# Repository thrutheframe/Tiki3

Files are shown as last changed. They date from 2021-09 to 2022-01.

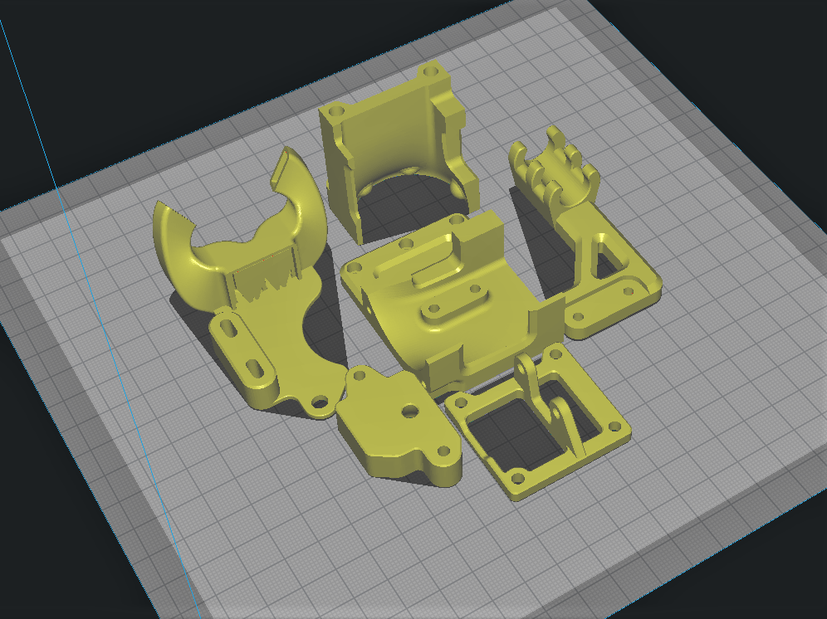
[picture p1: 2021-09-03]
3_2 Print orientation.png

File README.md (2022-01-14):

Tiki3 Gen3 2

# Tiki3 (version 3.2)

<b>Update 14 Jan 2022: </b> ADXL from Aliexpress shops are smaller (16mmx 20.5mm). So I have edited the body top to be able to mount them.  
\
\
\
\
<b>Update 14 Oct 2021: </b> 
- Updated fan duct design to V2. used a CFD simulation to check for air path.
- Added body_top with adxl mount. Mounting holes are 19mm apart. Please measure your adxl to check fitting. Will only work with fan_duct V2. 
body_top adxl04

\
\
<b>Update 12 Sep 2021: </b> shorter version of cable relief added. reduce by 20mm from the original. This is to prevent the cable from hitting the top bar during tall prints. 
\
\
<b>Introduction</b>\
A mount and fan duct system for Creality Ender 3/3pro/3V2 and Ender 5/5plus

This mount and fan duct system is designed for the hotend carriage of some Creality Ender machines.  
- Ender 3/3pro/3V2
- Ender 5/5pro/5plus

Hotend that has been designed for:
- Creality stock CR10 hotend (tested)
- Mellow NF-Zone CR10 (tested)
- Mellow NF-Smart 
- MicroSwiss All Metal and clones
- Red Lizard (need mod)
 
Tiki3 can be used as direct drive system with the Orbiter V1.5 or in a bowden configuration (No need to print "3_2 Orbiter bracket.stl" for bowden config)

A 5015 fan is required as the stock 4010 fan is underpowered for a dual fan duct system. 
 
Please see the other files for print orientation and BOM of screws and nuts required. 
 
There are many mount and fan duct system out there, what I think differs mine from others is the design focus on:
- Printability
- Functionality
- Modular system
 
As with all one-man-show, I would need the help of the community use/test this system and provide constructive suggestion to help me improve the existing design. 
Thank you for visiting my github page. 

I have to give credit where credit was due, so here goes: 

<b>CREDITS:</b>

My wife, for putting up with me as I dive into this insanity of mine. 

20four80five: https://www.thingiverse.com/thing:3354741
For first planting the idea of a side mount cooling fan and front mount part cooling fan

Hangtight: https://www.thingiverse.com/thing:4725293
For using his fan duct in version 3.1 when I was still learning Fusion360 and basing some of the design from him work as they are good.

lorinczroby: https://www.thingiverse.com/thing:4725897
For designing the Orbiter which I used for the direct drive design.

Grabcad community for coming up with all the STEP files that I need ie; 5015, 4010, BL touch, etc

Mellow for sharing with me the STEP file of their NF-Zone hotend. 

Thingiverse and anyone/organisation that I forgot to give credit to.

Please do share your make on Thingiverse: https://www.thingiverse.com/thing:4949727

<b>FAQs:</b>

Q: Is there any major design changes between this version (3.2) and the previous versions that are uploaded on Thingiverse?

A: Most of the changes structual improvements, but the position of the mounting holes are the same. The major changes is the fan duct. but it will still fit the over versions as the mounting holes are the same. 

Q:Will there be a design for V6 /Dragon hotend?

A: Yes. I am working on the Dragon version. You can download it from https://github.com/thrutheframe/Tiki3_Dragon. The V6 version is a bit tricky. so it will take time.

Q: Would you be able to include a custom design for bracket/fan duct/holder etc etc?

A: Due to my engineering background and training, I have a habit to print and test the designs to my level best before I release them. Without the actual item (or part that are close the the same dimensions) I would not be able to do that. Either I can borrow the items from friends or someone/company is willing to sponsor me the item. There is not much I can do. 

Q: Will this system fit the Sovol/Tronxy/TwoTrees etc etc?

A: Honestly, I would not know as I do not have those printers to work with.

Q: Would you release the STEP file for others to remix your design?

A: I asked this question once and the answer was "if u can remix it, u can design it on your own". He was kindof an asshole, but he was not wrong either. That is why I ended up designing my own mount system. I prefer not to be an asshole, but I am cheeky. Hence, I would release the STEP files for the body and BL bracket, which will be a good foundation to built your own version/remix.  

Q: Did you test print it in PLA? How did you get even get such specific numbers? "...I find stuff like this very misleading with serious potential to cause damage to printers when people try to do it..." 

A: I try my best to answer questions pertaining to the design. Constructive suggestions and contributions to the design are greatly apperciated. Please be polite and nice. 

Q: How accurate is the CFD simulation on your fan duct? Did u consider turbulance of of the 5015? Did u take into account of hotend movement? etc etc.

A: My basic CFD simulation of the particles movement (air) is to provide a validation that the air is directed under the nozzle when designing the fan duct. There are many other parameters that I would not know. tbh, it's a fanduct for 3D printer, not a cooling system of a nuclear plant... so take a chill pill and dun go karen/kevin on me. 

Q: Why do you add a heat sink to your motor? it is counter-productive as it add weight? 

A: Simple. I like it. 

Q: Why it is called Tiki3

A: Tiki was the name of our family dog. He passed away several years ago and we still miss him dearly. So I named this system after him. 

<b>Contributions</b>\
 My 3D printing hobby is running on Fun-Funds which is usually in fumes state. Contribution to this funds are from small print jobs, servicing 3D printers and the once-in-a-blue-moon tip to my paypal.me account. If you like using this system and would like to really thanks me, a $2 coffee tip will be greatly appreciated (I like coffee). Thank you. https://www.paypal.com/paypalme/shannonheng

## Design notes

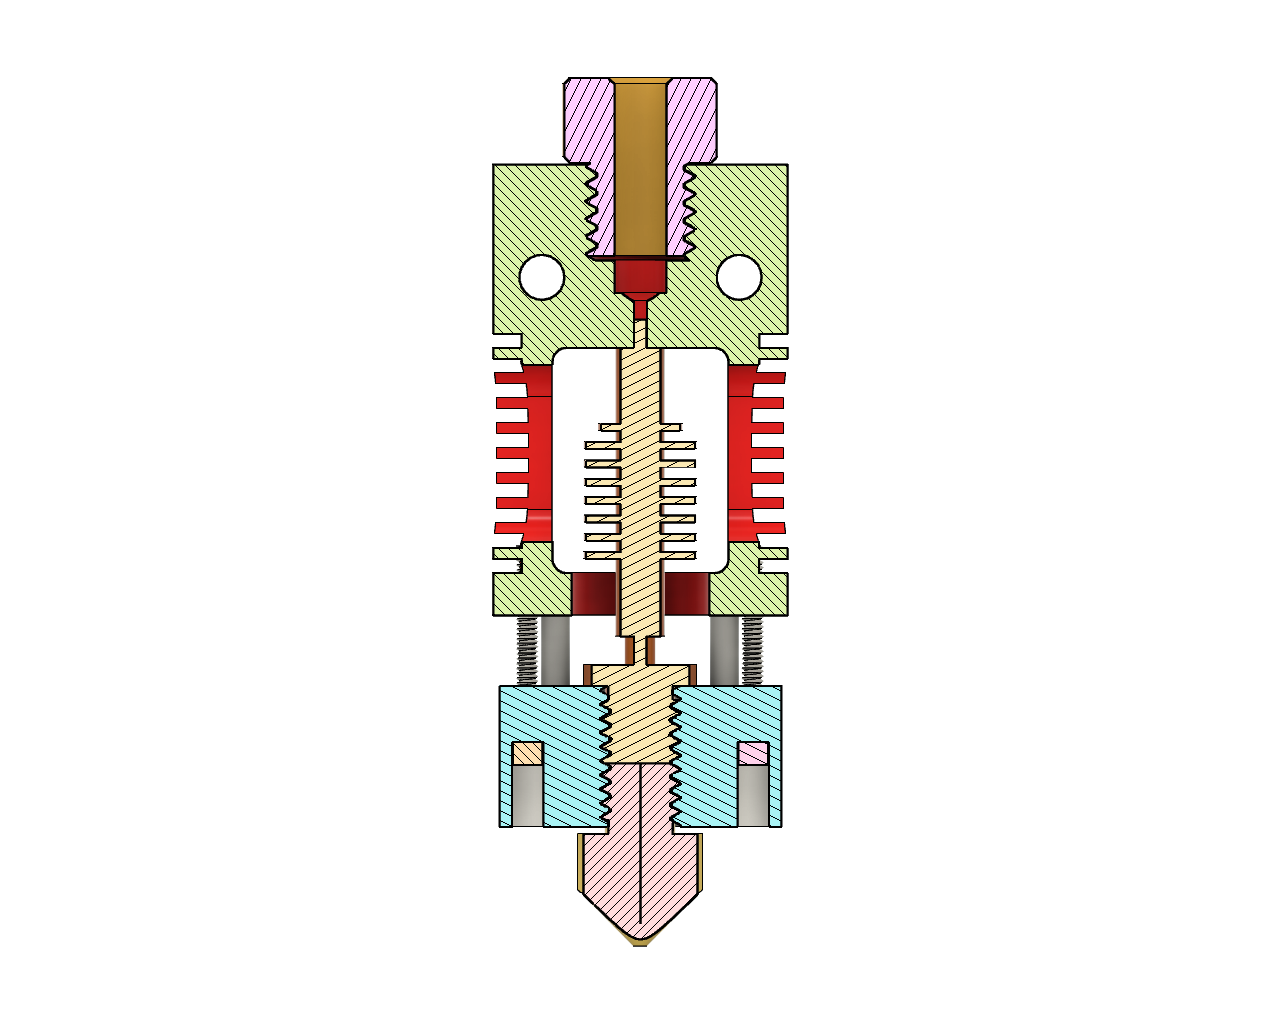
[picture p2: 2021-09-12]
Red Lizard adapter/adapter image 02.png

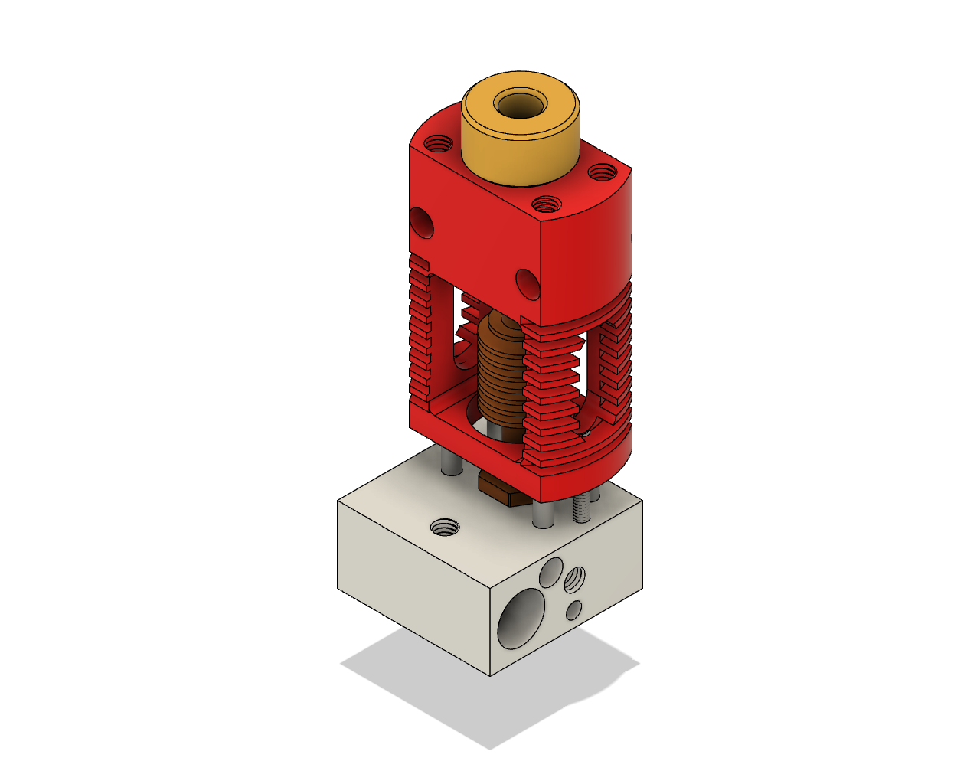
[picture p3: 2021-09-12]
Red Lizard adapter/adapter image 01.png

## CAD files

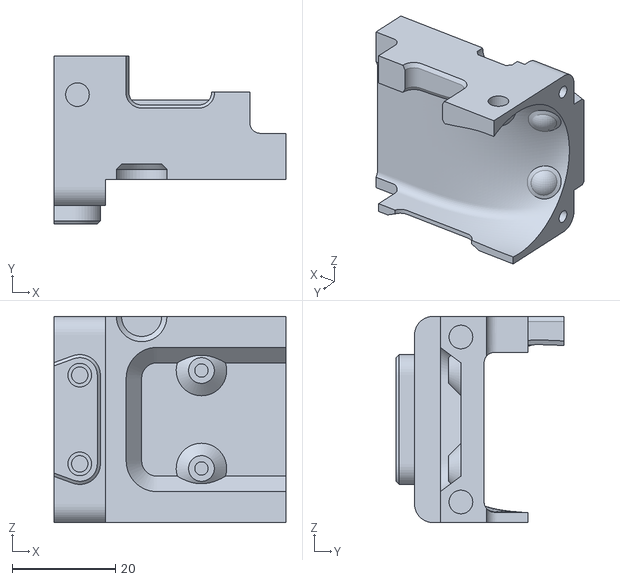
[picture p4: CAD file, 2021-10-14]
3_2 Body for brass inserts/3_2 Body_top adxl.stl
45.0 x 32.6 x 40.0

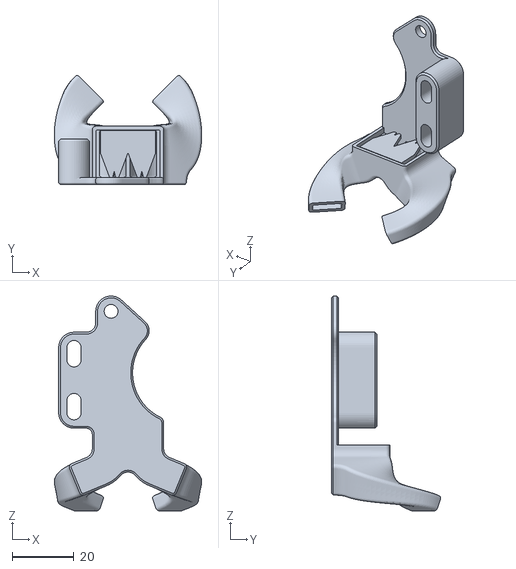
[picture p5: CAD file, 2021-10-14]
3_2 other parts/3_2 Fan_duct V2.stl
47.9 x 35.5 x 69.9

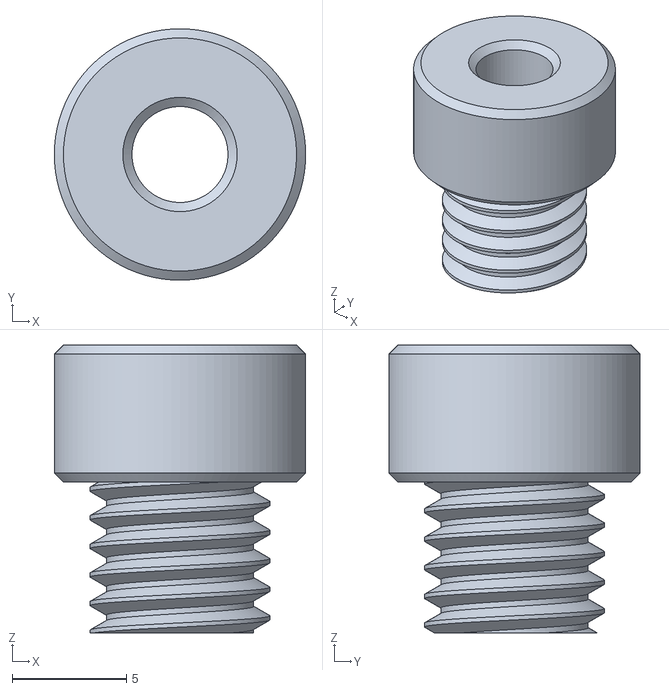
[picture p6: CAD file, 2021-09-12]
Red Lizard adapter/red lizard adapter 01.stl
11.0 x 11.0 x 12.6

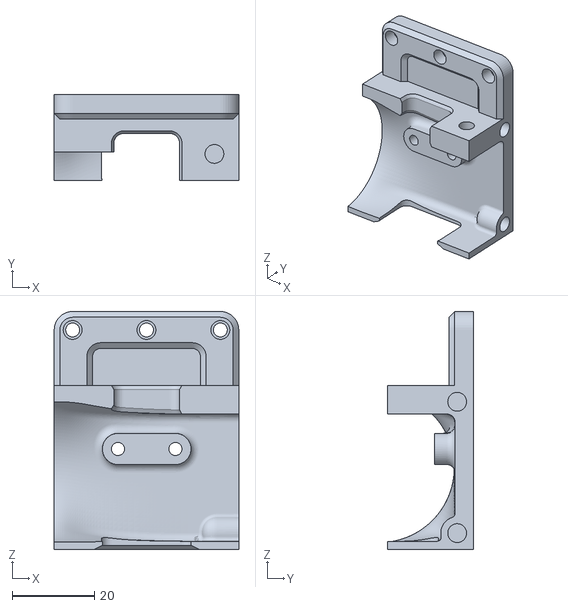
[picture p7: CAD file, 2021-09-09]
3_2 Body for brass inserts/3_2 Body_base.stl
45.0 x 21.0 x 58.0

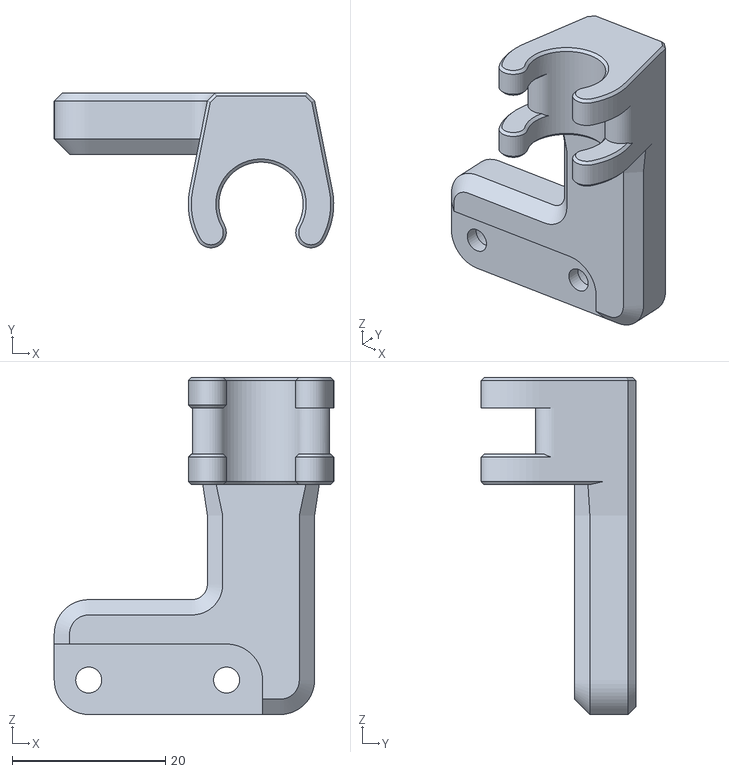
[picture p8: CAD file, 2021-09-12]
3_2 other parts/3_2 Cable relief short version.stl
36.5 x 20.2 x 44.0

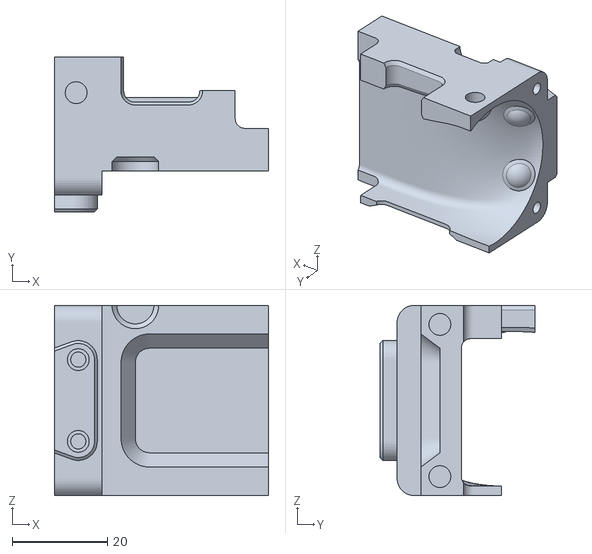
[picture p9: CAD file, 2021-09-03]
3_2 Body for brass inserts/3_2 Body_top.stl
45.0 x 32.6 x 40.0

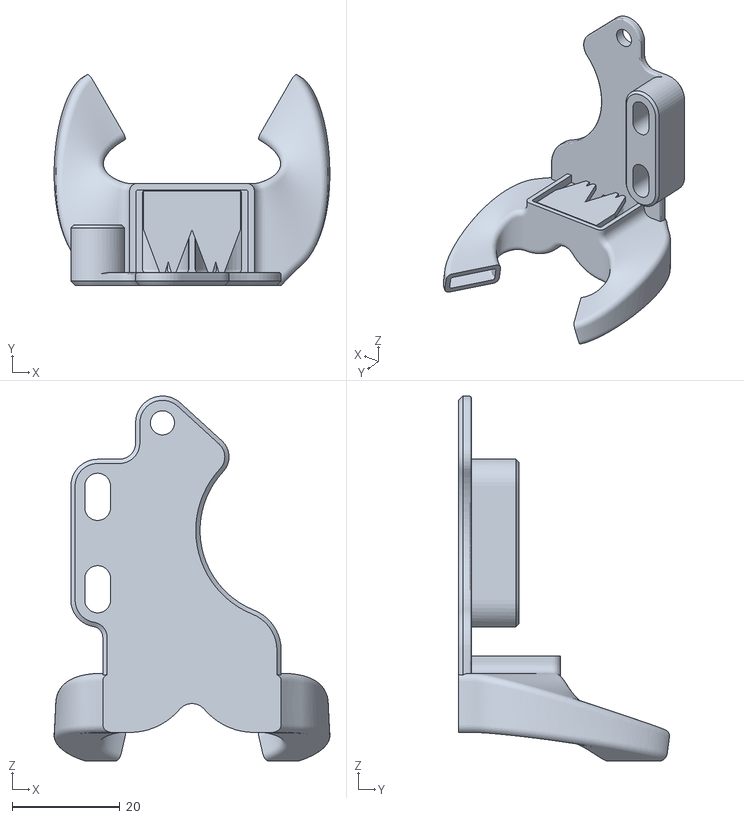
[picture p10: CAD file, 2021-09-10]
3_2 other parts/3_2 Fan duct.stl
51.3 x 39.3 x 67.9

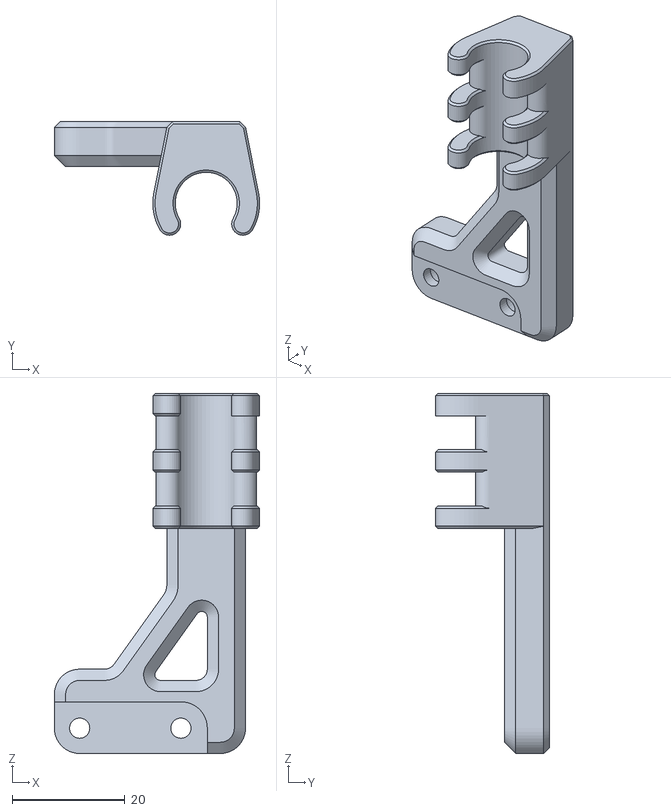
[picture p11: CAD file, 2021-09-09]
3_2 other parts/3_2 Cable relief.stl
36.5 x 20.2 x 64.0

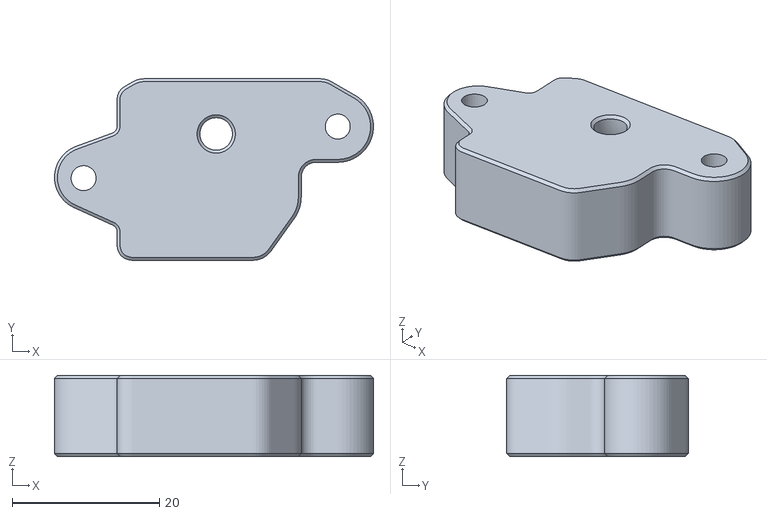
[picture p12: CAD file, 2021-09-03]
3_2 other parts/3_2 Orbiter bracket.stl
43.3 x 24.6 x 11.0

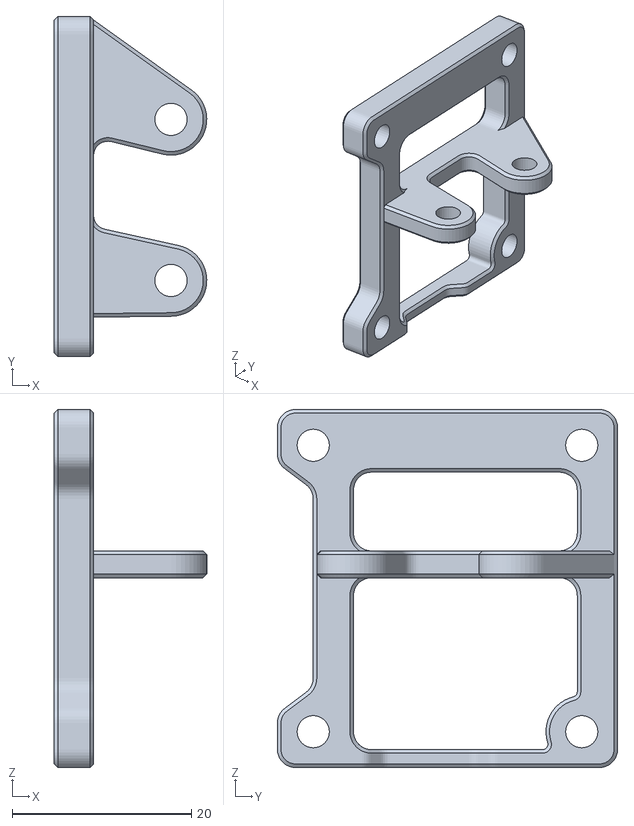
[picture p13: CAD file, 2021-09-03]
3_2 other parts/3_2 BLT bracket Mk8.stl
17.0 x 38.0 x 40.0

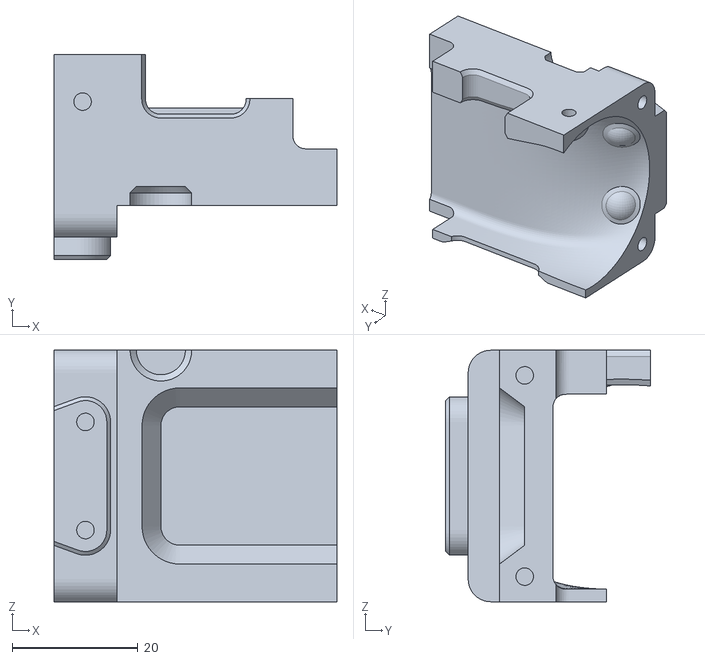
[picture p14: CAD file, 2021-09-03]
3_2 Body for M3 self-tap/M3 3_2 Body_top.stl
45.0 x 32.6 x 40.0

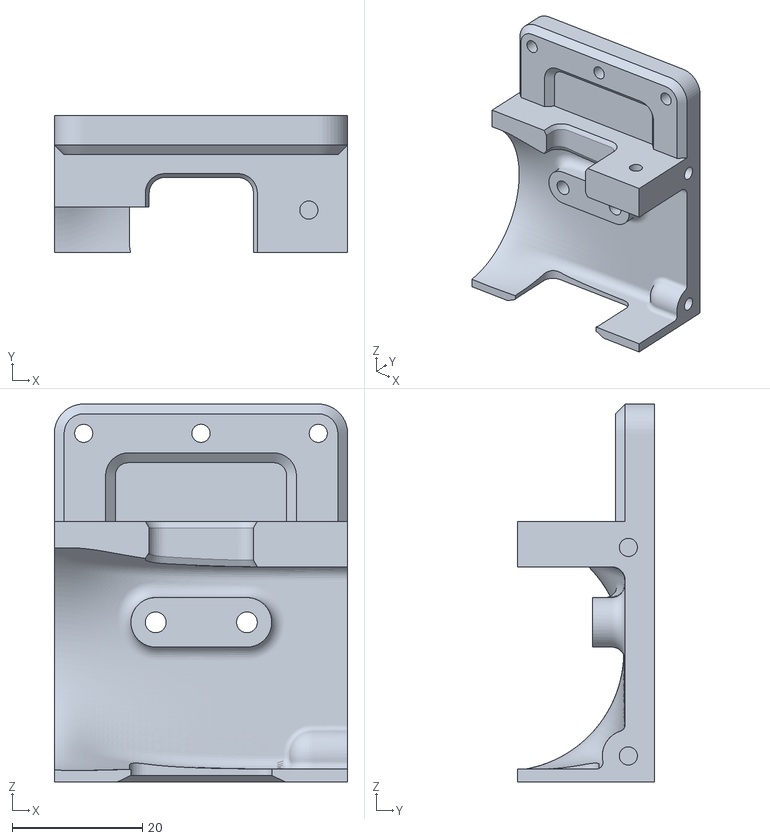
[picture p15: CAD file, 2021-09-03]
3_2 Body for M3 self-tap/M3 3_2 Body_base.stl
45.0 x 21.0 x 58.0

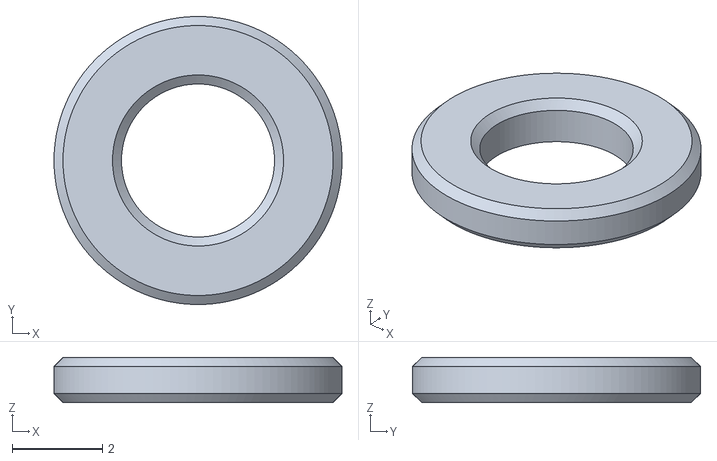
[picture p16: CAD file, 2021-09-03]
3_2 other parts/washer_1mm.stl
6.40 x 6.40 x 1.00

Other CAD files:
3_2 Body for M3 self-tap/3_2 Body_top adxl from Aliexpress.stl
3_2 Body for M3 self-tap/M3 3_2 Body_top adxl from Aliexpress.stl
3_2 Body for M3 self-tap/M3 3_2 Body_top adxl.stl

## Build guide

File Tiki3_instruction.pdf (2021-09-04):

# (version 3.2)

Mount and fan duct system for Creality Ender 3/3pro/3V2 and

Ender 5/5plus using Mk8 hotend

Note: This installation manual is still a work in progress.

- Layer height: 0.2mm
This mount is design with a layer height of 0.2mm taken into consideration. Hence printing in 0.16mm or 0.12mm may not be as accurate.
- Filament: PLA+, PETG, ABS, Nylon, etc
I have tested prints in PETG, CF PETG and PLA+. While printing in normal PLA will also work, the body may warp if hotend temperature is above 230°C.
- Silicon sock must be used for this mount to work, else the fan duct will cause a thermal runaway.
- Support are needed for “3_2 Body_base.stl” and “3_2 Body_top.stl”. If you are using Cura, support angle can be set to 60 degrees to prevent unnecessary support at the top.

Installing “3_2 Body_base” and hotend.

Installing “3_2 Body_top” with 4010 fan

Install “3_2 BLT Bracket” and BL Touch

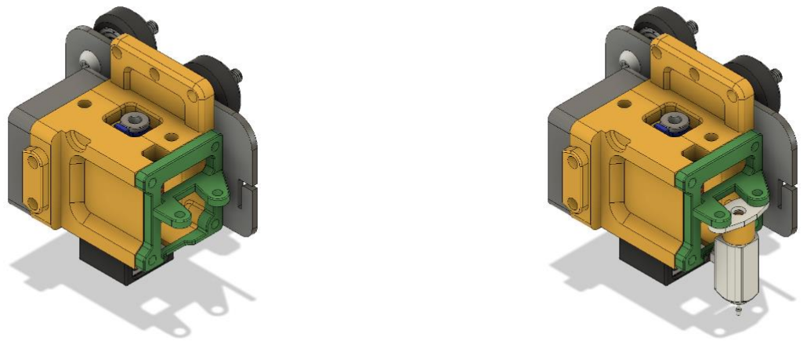
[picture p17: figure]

Install “3_2 Cable relief”

Install “Orbiter bracket” + Orbiter and ptfe tube

Removing bridging support on “3_2 Fan_duct”

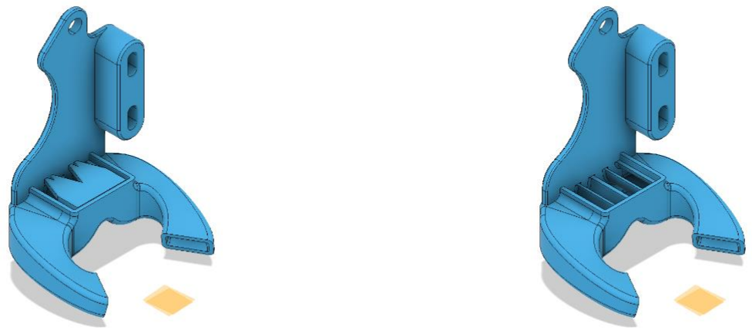
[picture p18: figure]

Install 5015 fan onto “3_2 Fan_duct”

Install “3_2 Fan_duct” on “3_2 Base_top”

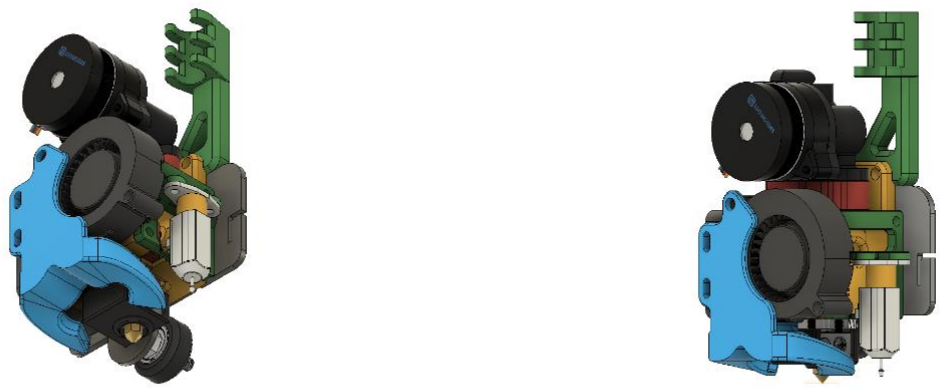
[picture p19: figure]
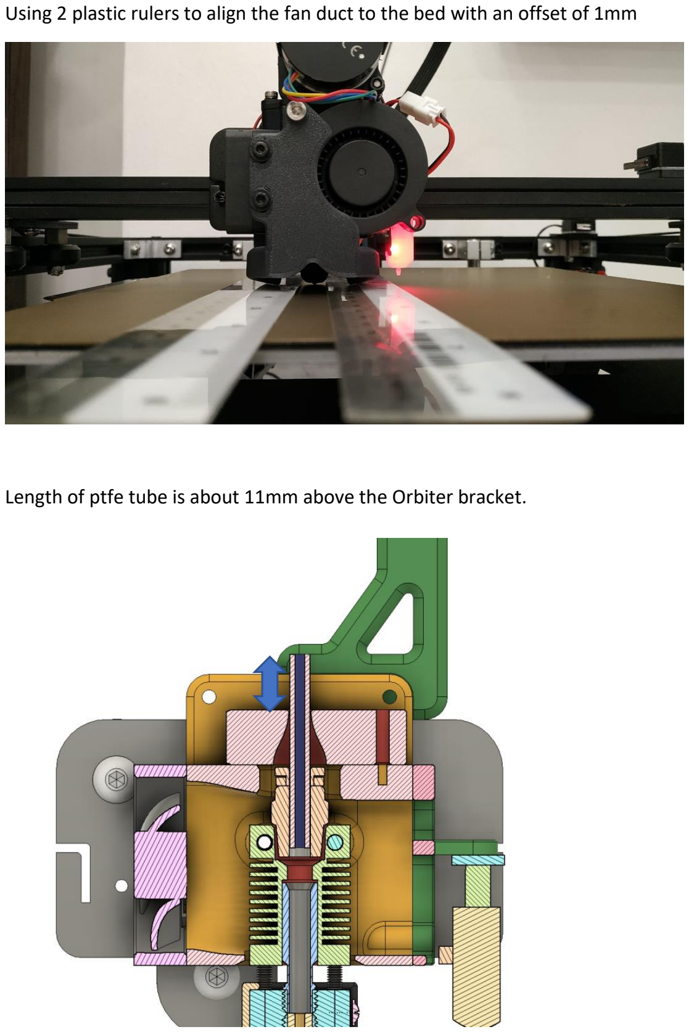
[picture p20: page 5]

Using 2 plastic rulers to align the fan duct to the bed with an offset of 1mm

Length of ptfe tube is about 11mm above the Orbiter bracket.

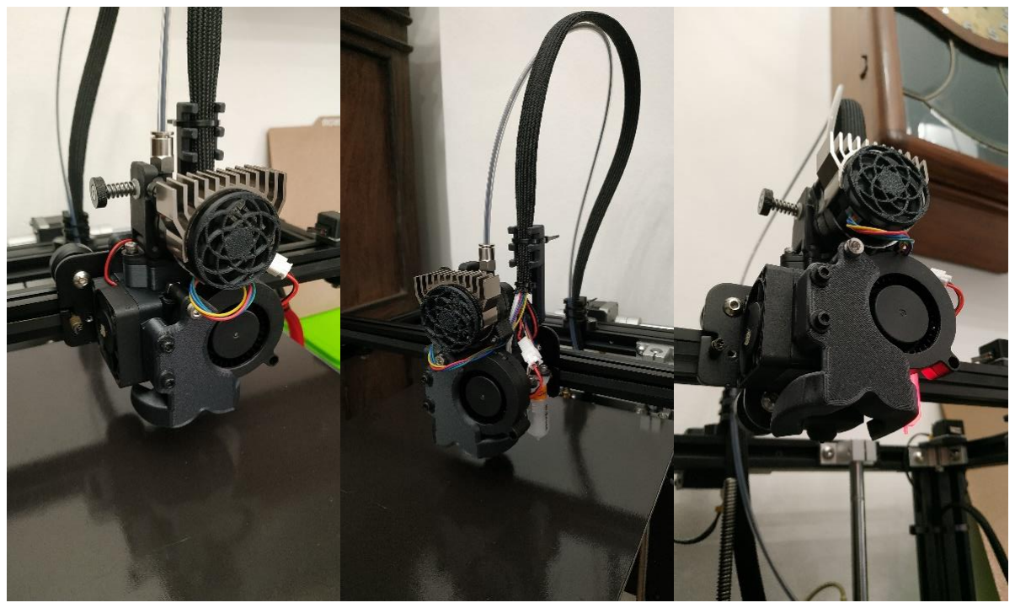
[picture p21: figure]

Probe XY Offset Values: X=35.5 Y=-5

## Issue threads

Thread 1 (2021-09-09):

Red lizard

MichaelAronsen, 2021-09-09:
So I have a few red lizard hotends, but they have a screw in fitting for the ptfe tube that is too big, have you had your hands on a red lizard hotend?

thrutheframe, 2021-09-11:
I do not have a red lizard hotend, but I understand what you are talking about. The V6 fitting is too big. I do have a prototype replacement adapter designed to solve the issue. Would you like to print it and try to see if this solution fits? thanks

https://github.com/thrutheframe/Tiki3/tree/main/Red%20Lizard%20adapter

MichaelAronsen, 2021-09-11:
Thanks, will print it tonight.

I tinkercad'ed a version that sort of works, but I'm sure this is better.

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

MichaelAronsen, 2021-09-11:
So, it fits and lets the red lizard fits in the mount.

However, the bowden tube can slide out which isnt great.

I've attached the mangled stl's that I made with tinkercade to enlarge the
holes in the mount to fit the red lizard.

On Sat, Sep 11, 2021 at 5:25 PM Michael Aronsen ***@***.***>
wrote:

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

thrutheframe, 2021-09-12:
for the adapter to work,
1. the length of the ptfe tube must be slightly longer (0.5mm). When the orbiter is mounted, there will be a compression where the tube will be held in place.
2. The hole on the adapter need to be snug. I relooked my design and realise I gave a little too much allowance. I have change it from 4.4mm to 4.2mm (0.2mm is to compensate for any shrinkage after print) This shold help in the fitting.

I have also included the STEP and f3d files of the adapter if anyone wants to do any change to it.

MichaelAronsen, 2021-09-12:
Thanks!

I'm starting it out in a bowden setup with a voron m4 extruder on my ender
3, so need the bowden to be really secured..

On Sun, Sep 12, 2021 at 6:21 AM Thrutheframe ***@***.***>
wrote:

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

thrutheframe, 2021-09-14:
ic. the STEP file of the body is available for editing to make the opening larger for the V6 attachment. I will close this issue as it is more or less solved. thanks

Closed 2021-09-14.

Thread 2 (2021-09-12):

Cable Relief too long

Ramrawd, 2021-09-12:
Hi there,

Really appreciate your work on this.

On my setup with an ender 3 v2 the Cable Relief is too long for taller prints. It causes the cabling to get bunched up under the top bar and creates a lot of drag.

I've designed a shorter version of this part in TinkerCad. It's pretty rough but it gets the job done.

I also added a channel in the back for zip ties to go through.

You may want to consider creating a shorter version of the cable guide for instances like mine.

Thanks!
[3_2_Cable_relief_Short.zip](https://github.com/thrutheframe/Tiki3/files/7149001/3_2_Cable_relief_Short.zip)
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

thrutheframe, 2021-09-12:
Thank you for the feedback. I have designed a short version (20mm shorter) of the cable relief. U can download it from the folder.
https://github.com/thrutheframe/Tiki3/tree/main/3_2%20other%20parts

Ramrawd, 2021-09-12:
Perfect! Thanks so much for doing that!

Closed 2021-09-12.

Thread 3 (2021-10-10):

Fan Duct AirFlow Direction

Ramrawd, 2021-10-10:
Hi there, I love your design and I've been using it for a few weeks now, but my one issue with it is the part cooling fan blows more air behind my nozzle rather than right at it. I've noticed my overhang and bridging quality has decreased since moving to this design. This is in comparison to the 5015 single blower petsfang duct system. The petsfang blows air almost directly from the sides.

If the fan duct tips extended out a bit further I think that would help in directing the airflow inwards towards the extruder nozzle.

I've attached a picture of a very rough mockup I made in Tinkercad. Unfortunately, my cad skills are limited to Tinkercad at the moment so I'd have no idea where to even start with such complicated shapes.

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

Any thoughts on your experiences with the ducts and potentially extending them/changing their angle?

Thanks!

thrutheframe, 2021-10-11:
hi, thanks for the feedback, I double checked. your observation is correct. the airflow speed at the back of the nozzle is faster than that of the front. This is an oversight on my design where airflow around a gentle curve has less resistance than the tighter one, While I workout a revision of the design,

Could you help test an idea? can you install a 2mm washer between the duct and the body to bring the fan duct forward so that the airflow is point at the nozzle. thanks

Ramrawd, 2021-10-11:
Thanks for taking a look at this!

Here are pictures with the 2mm spacer added. Still hitting a bit behind the nozzle even with the spacers

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
.

thrutheframe, 2021-10-12:
I reworked the fan duct design to focus the air just under the nozzle and a clean exit to the back.

Ramrawd, 2021-10-12:
Would it be possible to move the airflow further forward in relation to the nozzle?

It appears the the biggest volume of airflow is still intercepting behind the nozzle.

Also, from my own curiosity, what software are you using to model the airflow and design these parts? It really looks impressive.

Thanks!

thrutheframe, 2021-10-13:
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

thrutheframe, 2021-10-13:
The design should be ready in 2-3 days for test prints. I am currently tweaking it to optimise for printing. I will be updating it along with a new body_top with adxl mount for klipper users.

Ramrawd, 2021-10-13:
Sounds great! I'll keep an eye out for it. Also what an awesome addition with the ADXL mount.

I ended up using an m3 screw in the empty screw hole next to the cable relief mount to mount my adxl. Ended up working well since the threads held in the petg. That said a dedicated location for the ADXL is a welcome addition!

Thanks again for all your hard work
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
!
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

Ramrawd, 2021-10-14:
Thanks for the uploads. I'll throw it on the printer now and see how it comes out.

Gonna need to solder some new connectors on the adxl to utilize the new mount location.

Ramrawd, 2021-10-15:
New fan position looks pretty good! Also, please excuse the print quality on the duct... trying out a new filament and don't have my settings  dialed in yet :)

Haven't had a chance to resolder my ADXL but there's a good amount of clearance to squeeze it in with the 90 deg pins.

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

thrutheframe, 2021-10-16:
thanks for the feedback. In my testing, the airduct works better with improved overhangs. Will consider issue resolved and be closing this thread.

Closed 2021-10-16.

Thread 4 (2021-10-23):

Removing duct support tip

marcfon, 2021-10-23:
I broke one duct while removing the supports. The mistake I made was to start removing it from the bottom with cutters.

On my second print I found that it's much easier when you just insert a small flat screwdriver in the gap between support and duct and lift the support a little. That makes them break off cleanly without risking breaking the duct. This might be helpful to add in the documentation.

Thanks a lot for this project!

Closed 2021-12-16.

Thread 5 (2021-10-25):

NF Zone fitting issue

marcfon, 2021-10-25:
I'm encountering an issue where the head of the [NF Zone V6](https://www.aliexpress.com/item/1005001648634333.html) hot end isn't fitting the back plate.

The gap in the head is 5.8mm while the backplate bar is 7.0mm thick.

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

Closed 2021-11-05.

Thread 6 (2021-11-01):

Idea - screw hole to access heatsink screws

pankleks, 2021-11-01:
Hello!

First of all awesome work - I just installed it - and looking forward to see performance.

One idea - in body top - there could be a 2 holes in areas to access heatsink mounting screws + hole for tiny screw to block heartbreak.

I don't think it would affect part structural strength but it would allow to access these screw (for inspection/tightening) without unmounting entire part.

Let me know what you think:)

thrutheframe, 2021-11-03:
in one of the first few prototype, I added the 2 holes (4mm) for accessing the heatsink. I got sporadic soft whistling sound when the fan start running. I have added the step files of the body. U may want to try it out by adding the holes.

pankleks, 2021-11-04:
thanks!

Closed 2021-11-04.

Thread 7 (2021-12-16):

Orbiter Extruder V2.0

Ramrawd, 2021-12-16:
Hi there,

Any chance you could add a new mounting bracket for the orbiter v2.0 extruder?

https://drive.google.com/drive/folders/1Kr8K3wX7nMKRvu9yo7Z1blTNQCAX_nJb

There are files for the new design.

Pre-orders are happening here: https://lukeslabonline.com/products/orbiter-v2-dual-drive-direct-extruder

Thanks!

thrutheframe, 2021-12-16:
As of now, I am not planning to design any mount for the Orbiter V2.0. Reasons:

1. The distance and position of mounting holes have changed with V2.0. Tiki3 will have to be redesigned from the ground up, as it uses the asymmetric mounting position of V1.5 to hold the bracket together.
2. My existing Orbiter V1.5 is working fine and I don't see myself buying the V2.0 as an upgrade.
3. I want to spend time and resources working on another design project.

If you are looking for a mounting system for V2.0, I think Robert will be uploading something soon and the maker of HeroMe had done one too.

Ramrawd, 2021-12-16:
Ah alright! Not a problem. Thanks for the explanation.

As always, really appreciate you work. I'll be keeping an eye out for other adaptations.

Have a good one!

thrutheframe, 2021-12-16:
I will be looking for testers for my other designer project if you are interested. u can message me on facebook.

Ramrawd, 2021-12-16:
Ah alright! I don't have a facebook account but I'll troll your githubs and see if anything new pops up. You're always welcome to message me if you'd like as well!

thrutheframe, 2021-12-16:
ic. sure, will msg u when it time to look for testers...lol thanks again

Closed 2022-01-14.

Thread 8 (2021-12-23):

No Fan duct in step file ?

yduf, 2021-12-23:
Hello there,

First thank you very much for providing a step file.
It helps me a a lot to play with it and remix the part.

A quick question: I am loading it with Freecad, but I don't see the fan-duct part in the step file ?
(while I see both fans). Is it normal ?

As I am just flipping 180° the orbiter, I don't need really need it. It is just that to have the final look in cad software, it is better since step files are rendered much better than stl in freecad.

Regards,

Yves

thrutheframe, 2021-12-28:
The step file only has the body and bl bracket for others to remix for different printer. The fanduct was omitted from the step file. Only stl available.

Closed 2022-01-14.

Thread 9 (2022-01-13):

Top part?

Arakon, 2022-01-13:
Is the top part that extends above the original X-Carriage necessary for operation/stability, other than mounting the cable guide? I use a titan extruder that is mounted on a printed plate from the back, which would most likely collide with that extension.

thrutheframe, 2022-01-14:
it is meant for cable guide and any other things that users might want to mount. Other thatn that it does not affects operations and stability.

Arakon, 2022-01-14:
Thank you.

Closed 2022-01-14.

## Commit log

2021-09-03 Delete Body for M3 self-tap directory
    naming error
    [M3 3_2 Body_base.stl, M3 3_2 Body_top.stl]
2021-09-03 Delete Body for brass inserts directory
    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
    [3_2 Body_base.stl, 3_2 Body_top.stl]
2021-09-06 fixing minor to M4 holes
    [3_2 Fan duct.stl]
2021-09-09 widening M3 holes to 3.4mm
    [3_2 Cable relief.stl]
2021-09-09 widening M3 to 3.4mm
    This is to compensate for slight shrinkage after cooling. For PLA an PETG.
    [3_2 Body_base.stl]
2021-09-09 Widening M3 to 3.4mm
    for brass insert
    [3_2 Body_base.stl]
2021-09-10 Increase mount holes size
    increase from 3.4mm to 4mm. Give allowance for horizontal adjustment.
    [3_2 Fan duct.stl]
2021-09-10 Increase mounting spacing and edit overall design
    [3_2 Fan duct.stl]
2021-09-11 An adapter for red lizard hotend
    [red lizard adapter 01.stl]
2021-09-12 editing ptfe hole diameter
    from 4.4mm to 4.2mm for a tighter fitting
    [red lizard adapter 01.stl]
2021-09-12 shorter version
    [3_2 Cable relief short version.stl]
2021-10-14 updated version of fan duct
    [3_2 Fan_duct V2.stl]
2021-10-14 with adxl mount
    [M3 3_2 Body_top adxl.stl]
2021-10-14 with mount for adxl
    [3_2 Body_top adxl.stl]
2022-01-14 body top for aliexpress ADXL
    [3_2 Body_top adxl from Aliexpress.stl, M3 3_2 Body_top adxl from Aliexpress.stl]
